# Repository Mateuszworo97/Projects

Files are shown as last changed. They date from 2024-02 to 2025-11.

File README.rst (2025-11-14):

About
-----

.. raw:: html

   <div style="text-align: justify;">

   <p>
   <strong>Apiary Water Dispensing System</strong> —  This is a device design whose purpose is to automatically supply bee water from an underground tank.
   In hard-to-reach places and with limited access to fresh water.
   The system's task is also to display current data regarding time, temperature and light intensity on the display.
   The system will enable the pump to be turned on at a specific time for a specific period of time.
   </p>

   <p>
   In the future, this project will be extended with new functionalities.
   Currently, I am working on two versions of the system that will reduce the size of the PCB and the number of components used.
   </p>

   <ul>
     <li><strong>Version 1:</strong> Uses the same components as the current version but in a smaller layout.</li>
     <li><strong>Version 2:</strong> Introduces new components to reduce PCB size while keeping the system expandable.</li>
     <li><strong>Version 3:</strong> Adds wireless data transmission using <em>LORAWAN</em> technology and integration with cloud platforms such as <em>ThingsBoard</em> or <em>TTN (The Things Network)</em>.</li>
   </ul>
   
   <p>
   One version will use the same components as the current one, but will be smaller in size.
   The second version will allow include new components that will reduce the size of the PCB board, but won't limit possibility of expended the system in the future.
   The PCB board will contains derivations for additional components that can be added later.
   The third version will expand the funtionality of the system with wireless data transmission using LORAWAN technology.
   Target of the system is to send data to cloud platform such as THINGSBOARD or TTN (The Things Network).
   Definitely, such action will investigate natural environment around device and bees activity.
   Currently, the first of version system has contributed to better understanding of bees behavior in hard to reach places with limited access to fresh water.
   I think that the third version of the system will be a great tool for beekeepers to monitor the environment around the beehive and bees activity.
   Above all, the system will allow to achieve the significant level of automation and considerably contributed to increase the capacity and coverage of the lorawan Network.
   </p>

Operation
------------

The system measures time, temperature, humidity, light intensity, battery voltage, 
value and direction of battery current flow, power consumered and delivered to battery,
Voltage of photovoltaic panel, value of photovoltaic panel.
The data is shown on the display.
By default, the pump is turned on for 1 minute. Every hour.
Using push buttons, we can increase the pump activation time from 1 to 59 minutes.
Using the buttons, we can also change the time at which the alarm will turn on (pump on).
The next time the alarm will turn on will be increased by the hour value displayed on the display.
we can delay the pump activation value from 1 to 16 hours.

Development
------------

1. Simplification 
2. Adding an automatic and manual control system
3. Enriching the project with wireless data transmission using  LORAWAN technology
4. Desiging a much smaller PCB
5. Creating own MPPT board

Block Diagram
------------
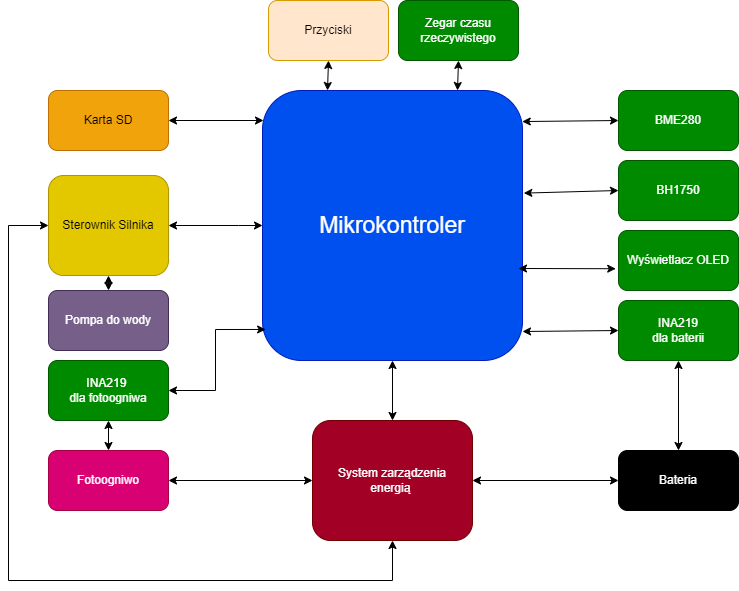
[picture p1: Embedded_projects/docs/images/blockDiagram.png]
Block Diagram


Visualization
------------
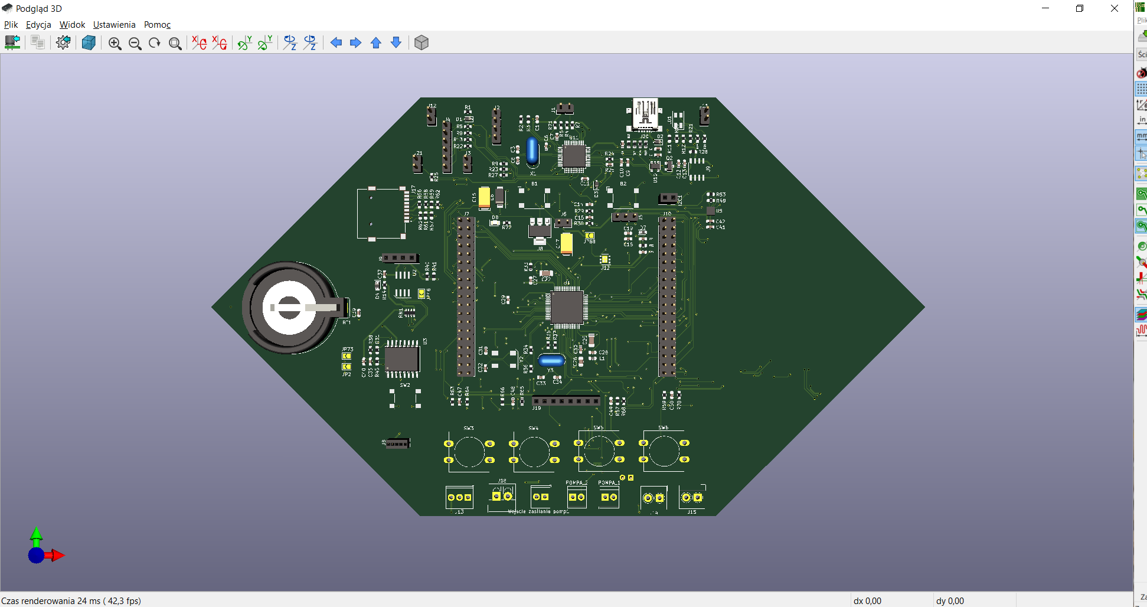
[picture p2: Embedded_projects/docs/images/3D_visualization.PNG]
Visualization


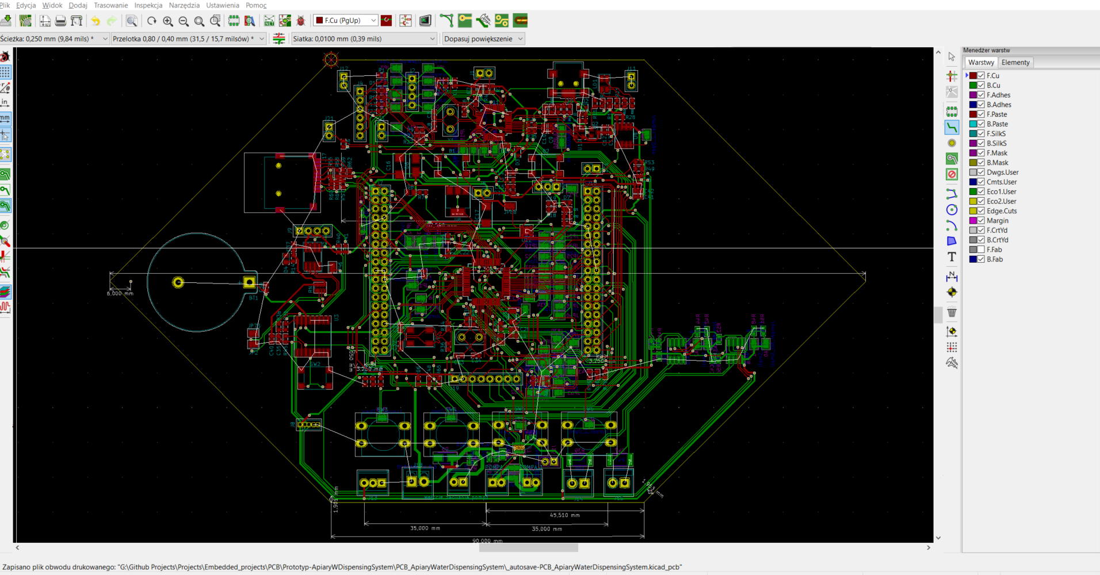
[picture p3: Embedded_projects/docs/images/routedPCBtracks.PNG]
Routed PCB tracks


Components
------------

Contains a list of components used to build the system

Refer to `docs/components.rst`.

Hardware
------------

Contains documentation of the sensors and components used.
-Diagram of the electronic system of the device.

Refer to `docs/hardware`.

Software
------------

-Diagram of the software nic system of the device.
Refer to `docs/software`.

License
------------

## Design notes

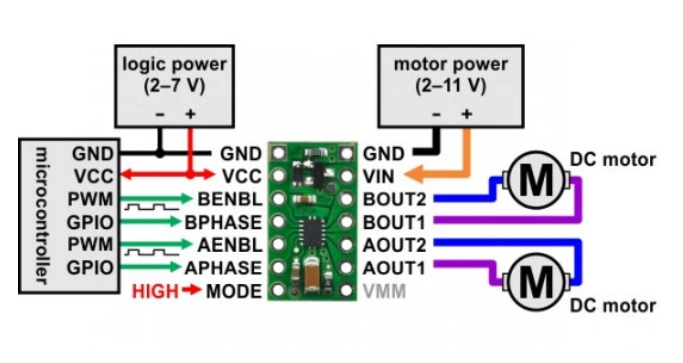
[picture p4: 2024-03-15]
Embedded_projects/docs/hardware/photos/drv8835.PNG

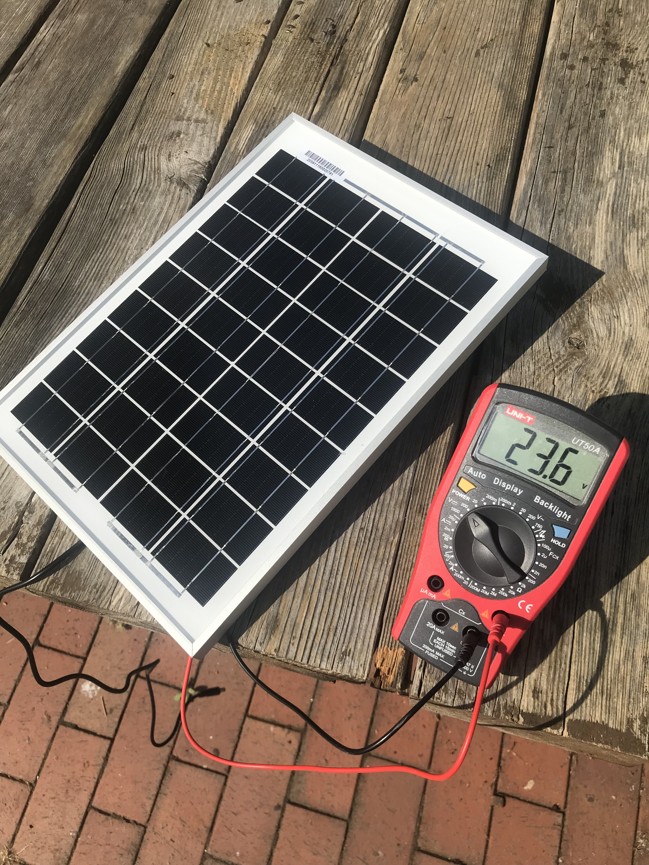
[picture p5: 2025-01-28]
Embedded_projects/docs/hardware/photos/open_circuit_pv.jpg

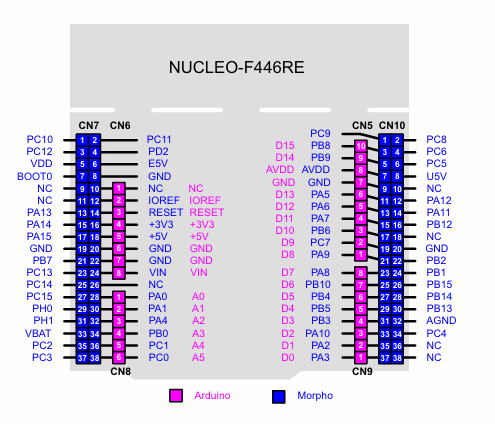
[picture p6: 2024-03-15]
Embedded_projects/docs/hardware/photos/nucleo-f446.PNG

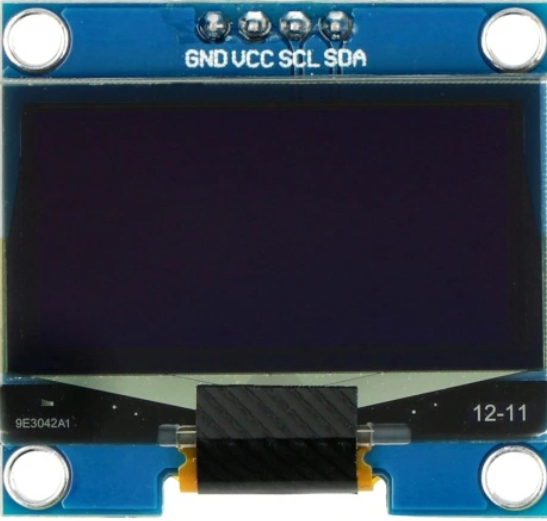
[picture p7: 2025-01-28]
Embedded_projects/docs/hardware/photos/ssd1306.PNG

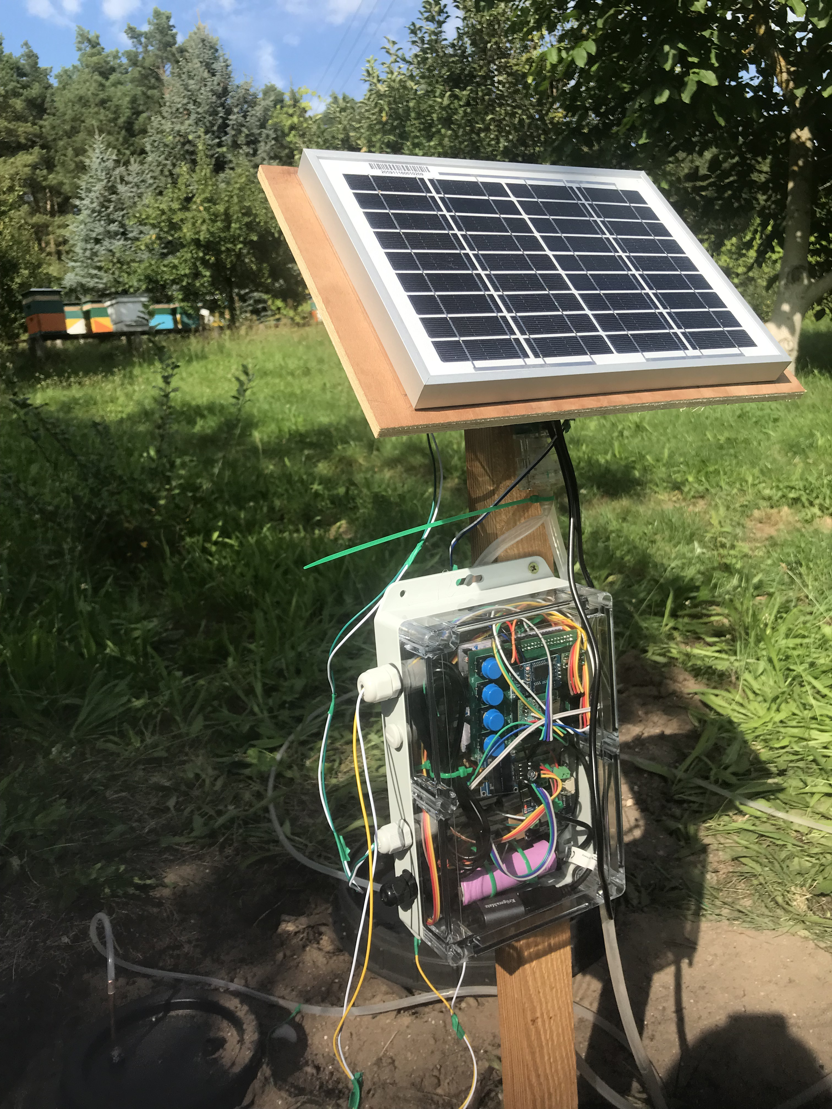
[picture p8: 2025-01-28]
Embedded_projects/docs/hardware/photos/urzadzenie_2.jpg

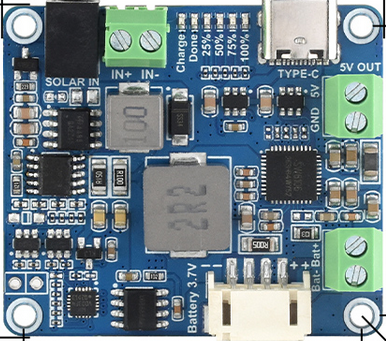
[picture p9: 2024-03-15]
Embedded_projects/docs/hardware/photos/solar_power_manager.PNG

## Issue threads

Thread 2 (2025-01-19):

Stm32WL development #4

Mateuszworo97, 2025-01-19:
the main goal of this issues will be creation project extension. Extension will be focused on long-range wireless communication, which will enable to be transferred to the cloud using a gateway device.

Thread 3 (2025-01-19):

Reducing the size of the PCB

Mateuszworo97, 2025-01-19:
the mian goal of this issue will be reduced the size of the PCB

Mateuszworo97, 2025-01-19:
- [ ]  adding two pumps connection
- [ ] control with 4 buttons
- [ ] external temperatures, humidity, pressure, light intensity sensor (Ds18b20)
- [ ] internal temperatures sensor
- [ ] SD card connector
- [ ] monitor air quality
- [ ]

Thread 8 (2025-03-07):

Switching the microcontroller to low power mode

Mateuszworo97, 2025-03-07:

Mateuszworo97, 2025-03-07:
Sleep mode advantages 👍

- [ ] retained RAM and working registers
- [ ] reduction of
- [ ] before entering sleep, suspend systick
- [ ] Sleep now (regardless of interruptions) or sleep exit (when all interrupts will be serviced)

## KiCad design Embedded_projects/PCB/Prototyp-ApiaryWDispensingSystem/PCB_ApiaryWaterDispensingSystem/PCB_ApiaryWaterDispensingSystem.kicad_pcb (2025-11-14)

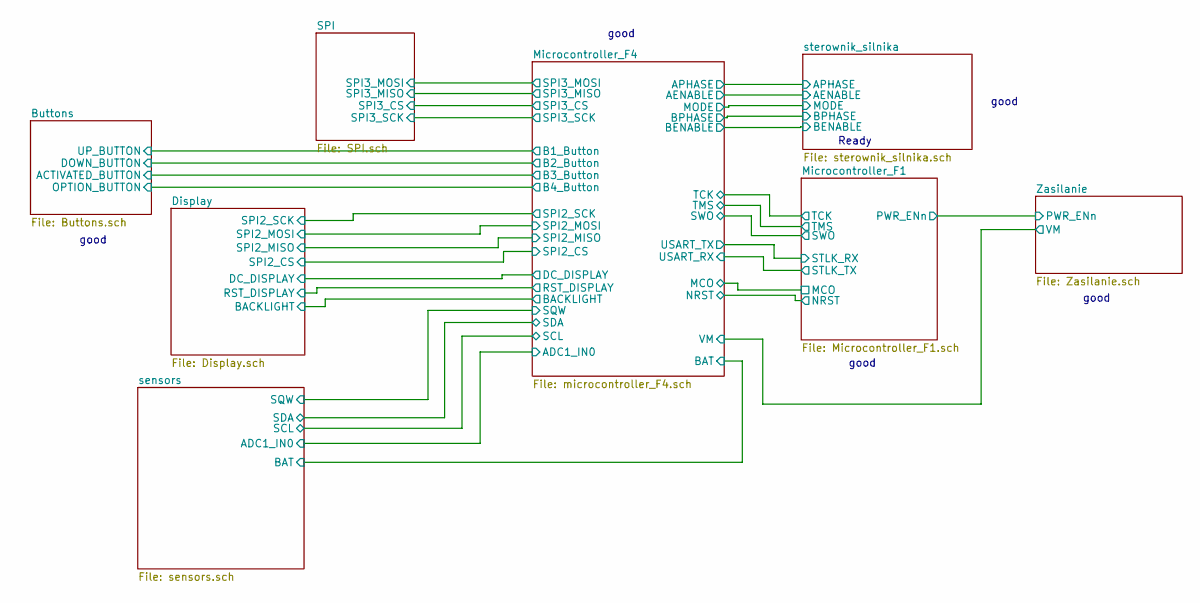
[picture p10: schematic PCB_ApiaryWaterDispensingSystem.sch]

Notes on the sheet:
Ready
good

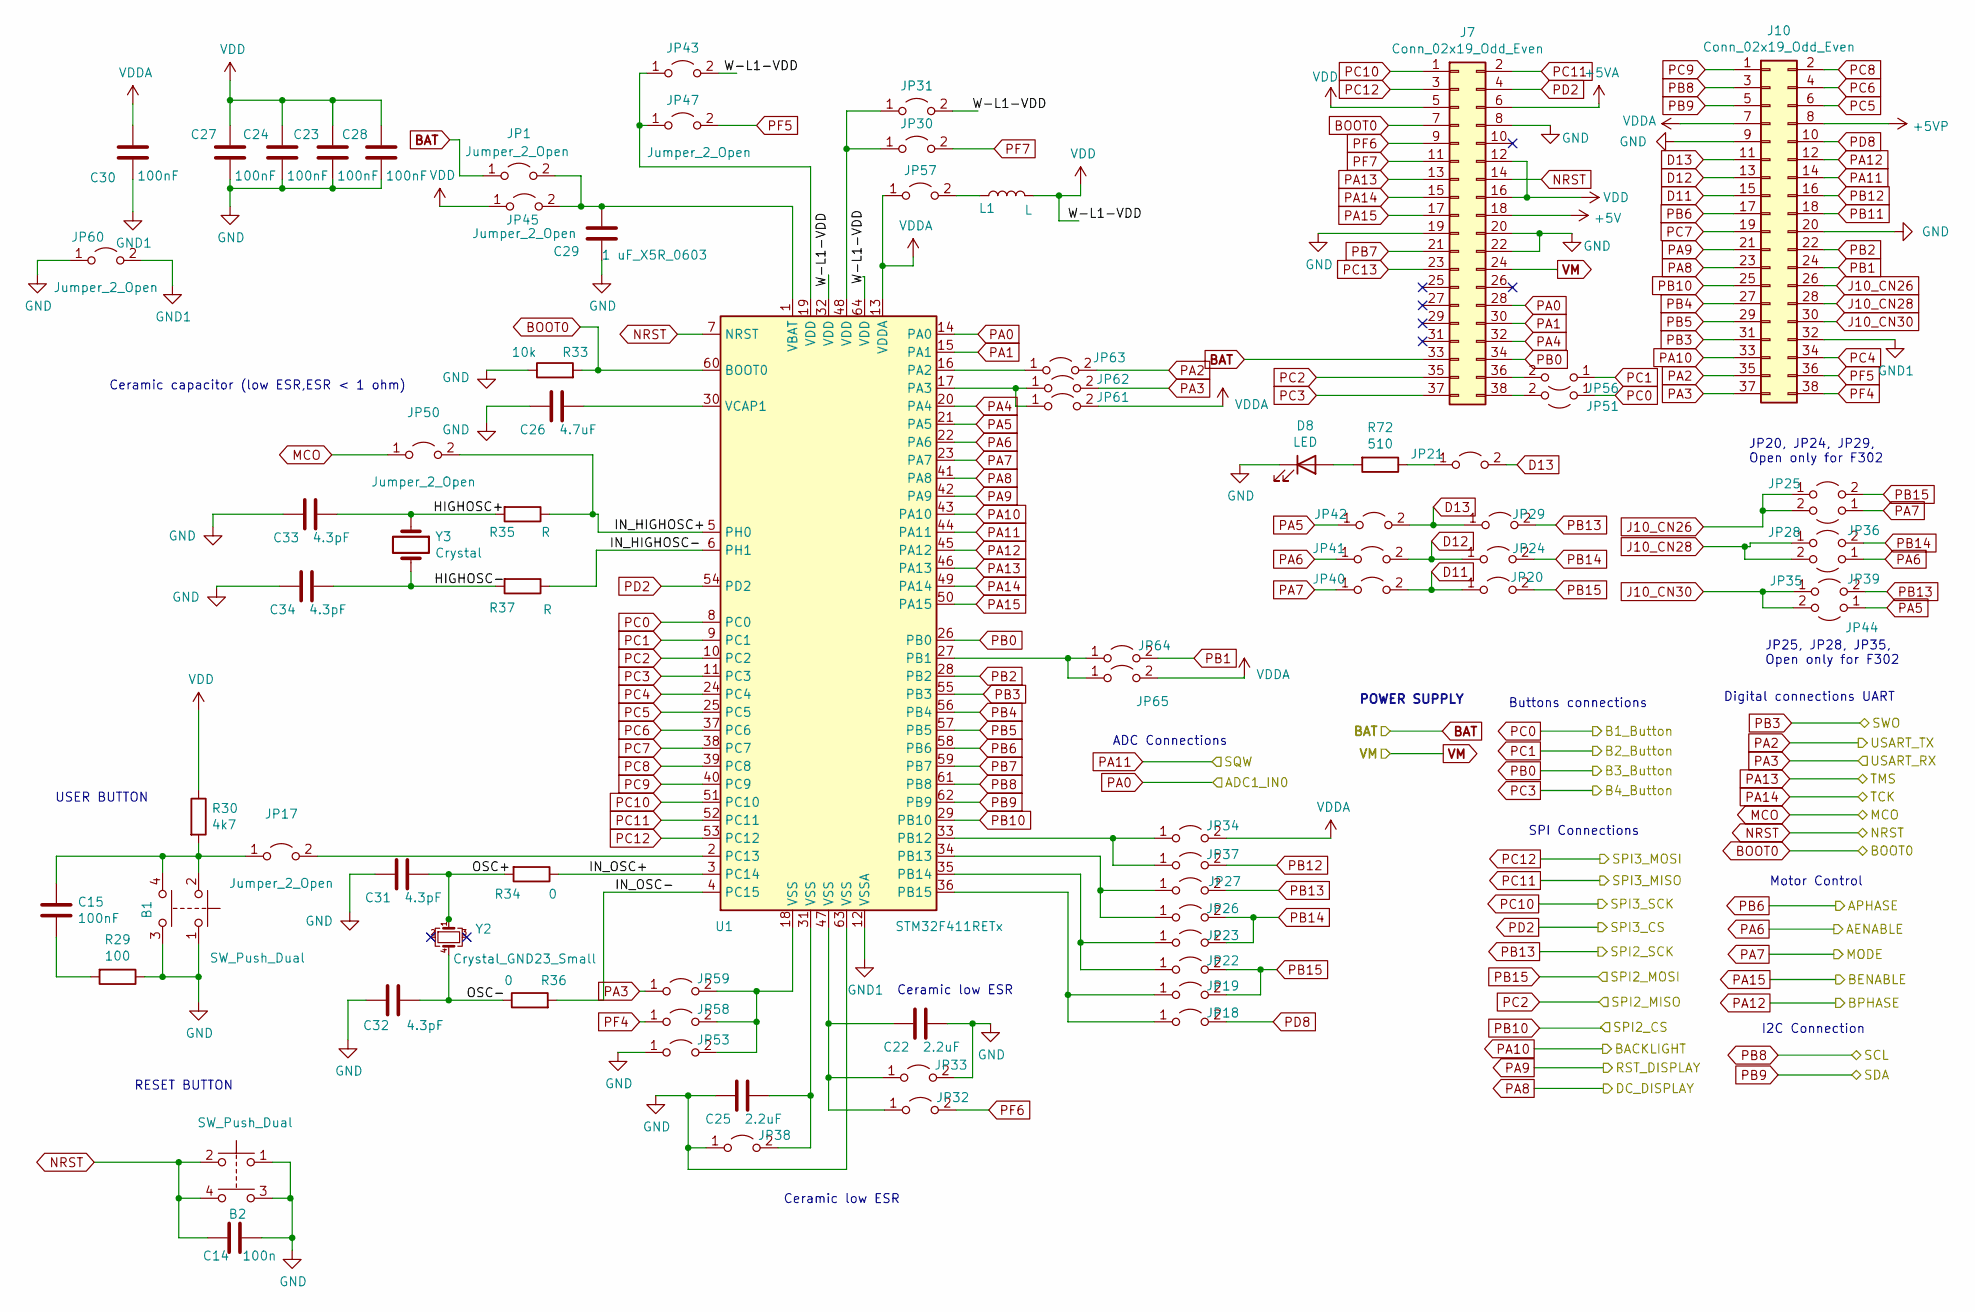
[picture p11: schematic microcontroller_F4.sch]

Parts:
B1, B2: SW_Push_Dual; SW_SPST_Omron_B3FS-100xP
C14: 100n; C_0603_1608Metric
C15, C23, C24, C27, C28, C30: 100nF; C_0603_1608Metric
C22, C25: 2.2uF; C_1206_3216Metric
C26: 4.7uF; C_0805_2012Metric
C29: 1 uF_X5R_0603; C_0603_1608Metric
C31, C32, C33, C34: 4.3pF; C_0603_1608Metric
D8: LED; LED_0805_2012Metric
J7, J10: Conn_02x19_Odd_Even; PinHeader_2x19_P2.54mm_Vertical
JP1, JP17, JP18, JP19, JP20, JP21, JP22, JP23, JP24, JP25, JP26, JP27, JP28, JP29, JP30, JP31, JP32, JP33, JP34, JP35, JP36, JP37, JP38, JP39, JP40, JP41, JP42, JP43, JP44, JP45, JP47, JP50, JP51, JP53, JP56, JP57, JP58, JP59, JP60, JP61, JP62, JP63, JP64, JP65: Jumper_2_Open; SolderJumper-2_P1.3mm_Open_TrianglePad1.0x1.5mm
L1: L; L_0603_1608Metric
R29: 100; R_0603_1608Metric
R30: 4k7; R_0603_1608Metric
R33: 10k; R_0603_1608Metric
R34, R36: 0; R_0603_1608Metric
R35, R37: R; R_0603_1608Metric
R72: 510; R_0603_1608Metric
U1: STM32F411RETx; LQFP-64_10x10mm_P0.5mm
Y2: Crystal_GND23_Small; ABS25-32768KHZ-6-T_Abracon
Y3: Crystal; Resonator-2Pin_W8.0mm_H3.5mm

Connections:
+5V: J7.18; also elsewhere on the board
+5VA: J7.6; also elsewhere on the board
+5VP: J10.8; also elsewhere on the board
/Microcontroller_F4/HIGHOSC+: C33.1, R35.2, Y3.1
/Microcontroller_F4/HIGHOSC-: C34.1, R37.2, Y3.2
/Microcontroller_F4/IN_HIGHOSC+: JP50.2 (B), R35.1, U1.5 (PH0)
/Microcontroller_F4/IN_HIGHOSC-: R37.1, U1.6 (PH1)
/Microcontroller_F4/IN_OSC+: R34.1, U1.3 (PC14)
/Microcontroller_F4/IN_OSC-: R36.2, U1.4 (PC15)
/Microcontroller_F4/OSC+: C31.1, R34.2, Y2.1
/Microcontroller_F4/OSC-: C32.1, R36.1, Y2.4
ADC1_IN0: J7.28, U1.14 (PA0); also elsewhere on the board
AENABLE: JP39.1 (A), JP41.1 (A), U1.22 (PA6); also elsewhere on the board
APHASE: J10.17, U1.58 (PB6); also elsewhere on the board
BAT: J7.33, JP1.1 (A); also elsewhere on the board
BENABLE: J7.17, U1.50 (PA15); also elsewhere on the board
BOOT0: J7.7, R33.2, U1.60 (BOOT0); also elsewhere on the board
BPHASE: J10.12, U1.45 (PA12); also elsewhere on the board
Backlight: J10.33, U1.43 (PA10); also elsewhere on the board
CLK: J7.1, U1.51 (PC10); also elsewhere on the board
CMD: J7.3, U1.53 (PC12); also elsewhere on the board
D11: J10.15, JP20.1 (A), JP40.2 (B)
D12: J10.13, JP24.1 (A), JP41.2 (B)
D13: J10.11, JP21.2 (B), JP29.1 (A), JP42.2 (B)
DAT0: J7.2, U1.52 (PC11); also elsewhere on the board
DAT3: J7.4, U1.54 (PD2); also elsewhere on the board
DC_DISPLAY: J10.23, U1.41 (PA8); also elsewhere on the board
GND: B1.1, B1.3, B2.1, B2.3, C14.1, C22.1, C23.1, C24.1, C25.2, C26.2, C27.1, C28.1, C29.1, C31.2, C32.2, C33.2, C34.2, D8.1 (K), J7.8, J7.19, J7.20, J7.22, J10.9, J10.20, JP33.2 (B), JP38.1 (A), JP53.1 (A), JP60.1 (A), R29.1, R33.1, U1.63 (VSS); also elsewhere on the board
GND1: C30.1, J10.32, JP60.2 (B), U1.12 (VSSA)
J10_CN26: J10.26, JP25.1 (A), JP36.2 (B)
J10_CN28: J10.28, JP28.1 (A), JP39.2 (B)
J10_CN30: J10.30, JP35.1 (A), JP44.2 (B)
MCO: JP50.1 (A); also elsewhere on the board
MODE: JP36.1 (A), JP40.1 (A), U1.23 (PA7); also elsewhere on the board
NRST: B2.2, B2.4, C14.2, J7.14, U1.7 (NRST); also elsewhere on the board
unnamed: B1.2, B1.4, C15.1, JP17.1 (A), R30.2
unnamed: C15.2, R29.2
unnamed: C22.2, JP32.1 (A), JP33.1 (A), U1.47 (VSS)
unnamed: C25.1, JP38.2 (B), U1.31 (VSS)
unnamed: C26.1, U1.30 (VCAP1)
unnamed: C29.2, JP1.2 (B), JP45.2 (B), U1.1 (VBAT)
unnamed: D8.2 (A), R72.2
unnamed: J7.36, JP56.2 (B)
unnamed: J7.38, JP51.2 (B)
unnamed: JP17.2 (B), U1.2 (PC13)
unnamed: JP18.1 (A), JP19.1 (A), U1.36 (PB15)
unnamed: JP21.1 (A), R72.1
unnamed: JP22.1 (A), JP23.1 (A), U1.35 (PB14)
unnamed: JP26.1 (A), JP27.1 (A), U1.34 (PB13)
unnamed: JP30.1 (A), JP31.1 (A), U1.48 (VDD)
unnamed: JP34.1 (A), JP37.1 (A), U1.33 (PB12)
unnamed: JP43.1 (A), JP47.1 (A), U1.19 (VDD)
unnamed: JP53.2 (B), JP58.2 (B), JP59.2 (B), U1.18 (VSS)
unnamed: JP57.2 (B), L1.1
unnamed: JP61.1 (A), JP62.1 (A), U1.17 (PA3)
unnamed: JP63.1 (A), U1.16 (PA2)
unnamed: JP64.1 (A), JP65.1 (A), U1.27 (PB1)
PA1: J7.30, U1.15 (PA1)
PA2: J10.35, JP63.2 (B); also elsewhere on the board
PA3: J10.37, JP59.1 (A), JP62.2 (B); also elsewhere on the board
PA4: J7.32, U1.20 (PA4)
PA5: JP42.1 (A), JP44.1 (A), U1.21 (PA5)
PA9: J10.21, U1.42 (PA9); also elsewhere on the board
PA11: J10.14, U1.44 (PA11); also elsewhere on the board
PA13: J7.13, U1.46 (PA13); also elsewhere on the board
PA14: J7.15, U1.49 (PA14); also elsewhere on the board
PB0: J7.34, U1.26 (PB0); also elsewhere on the board
PB1: J10.24, JP64.2 (B)
PB2: J10.22, U1.28 (PB2)
PB3: J10.31, U1.55 (PB3); also elsewhere on the board
PB4: J10.27, U1.56 (PB4)
PB5: J10.29, U1.57 (PB5)
PB7: J7.21, U1.59 (PB7)
PB8: J10.3, U1.61 (PB8); also elsewhere on the board
PB9: J10.5, U1.62 (PB9); also elsewhere on the board
PB10: J10.25, U1.29 (PB10); also elsewhere on the board
PB12: J10.16, JP37.2 (B)
PB13: JP27.2 (B), JP29.2 (B), JP35.2 (B); also elsewhere on the board
PB14: JP23.2 (B), JP24.2 (B), JP26.2 (B), JP28.2 (B)
PB15: JP19.2 (B), JP20.2 (B), JP22.2 (B), JP25.2 (B); also elsewhere on the board
PC0: JP51.1 (A), U1.8 (PC0); also elsewhere on the board
PC1: JP56.1 (A), U1.9 (PC1); also elsewhere on the board
PC2: J7.35, U1.10 (PC2)
PC3: J7.37, U1.11 (PC3); also elsewhere on the board
PC4: J10.34, U1.24 (PC4)
PC5: J10.6, U1.25 (PC5)
PC6: J10.4, U1.37 (PC6)
PC7: J10.19, U1.38 (PC7)
PC8: J10.2, U1.39 (PC8)
PC9: J10.1, U1.40 (PC9)
PD8: J10.10, JP18.2 (B)
PF4: J10.38, JP58.1 (A)
PF5: J10.36, JP47.2 (B)
PF6: J7.9, JP32.2 (B)
PF7: J7.11, JP30.2 (B)
VDD: C23.2, C24.2, C27.2, C28.2, J7.5, J7.12, J7.16, JP31.2 (B), JP43.2 (B), JP45.1 (A), L1.2, R30.1, U1.32 (VDD), U1.64 (VDD); also elsewhere on the board
VDDA: C30.2, J10.7, JP34.2 (B), JP57.1 (A), JP61.2 (B), JP65.2 (B), U1.13 (VDDA)
VM: J7.24; also elsewhere on the board

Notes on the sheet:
Ceramic capacitor (low ESR,ESR < 1 ohm)
Ceramic low ESR
RESET BUTTON
USER BUTTON
Buttons connections
Digital connections UART
SPI Connections
Motor Control
I2C Connection
JP25, JP28, JP35, Open only for F302
JP20, JP24, JP29, Open only for F302
POWER SUPPLY
ADC Connections

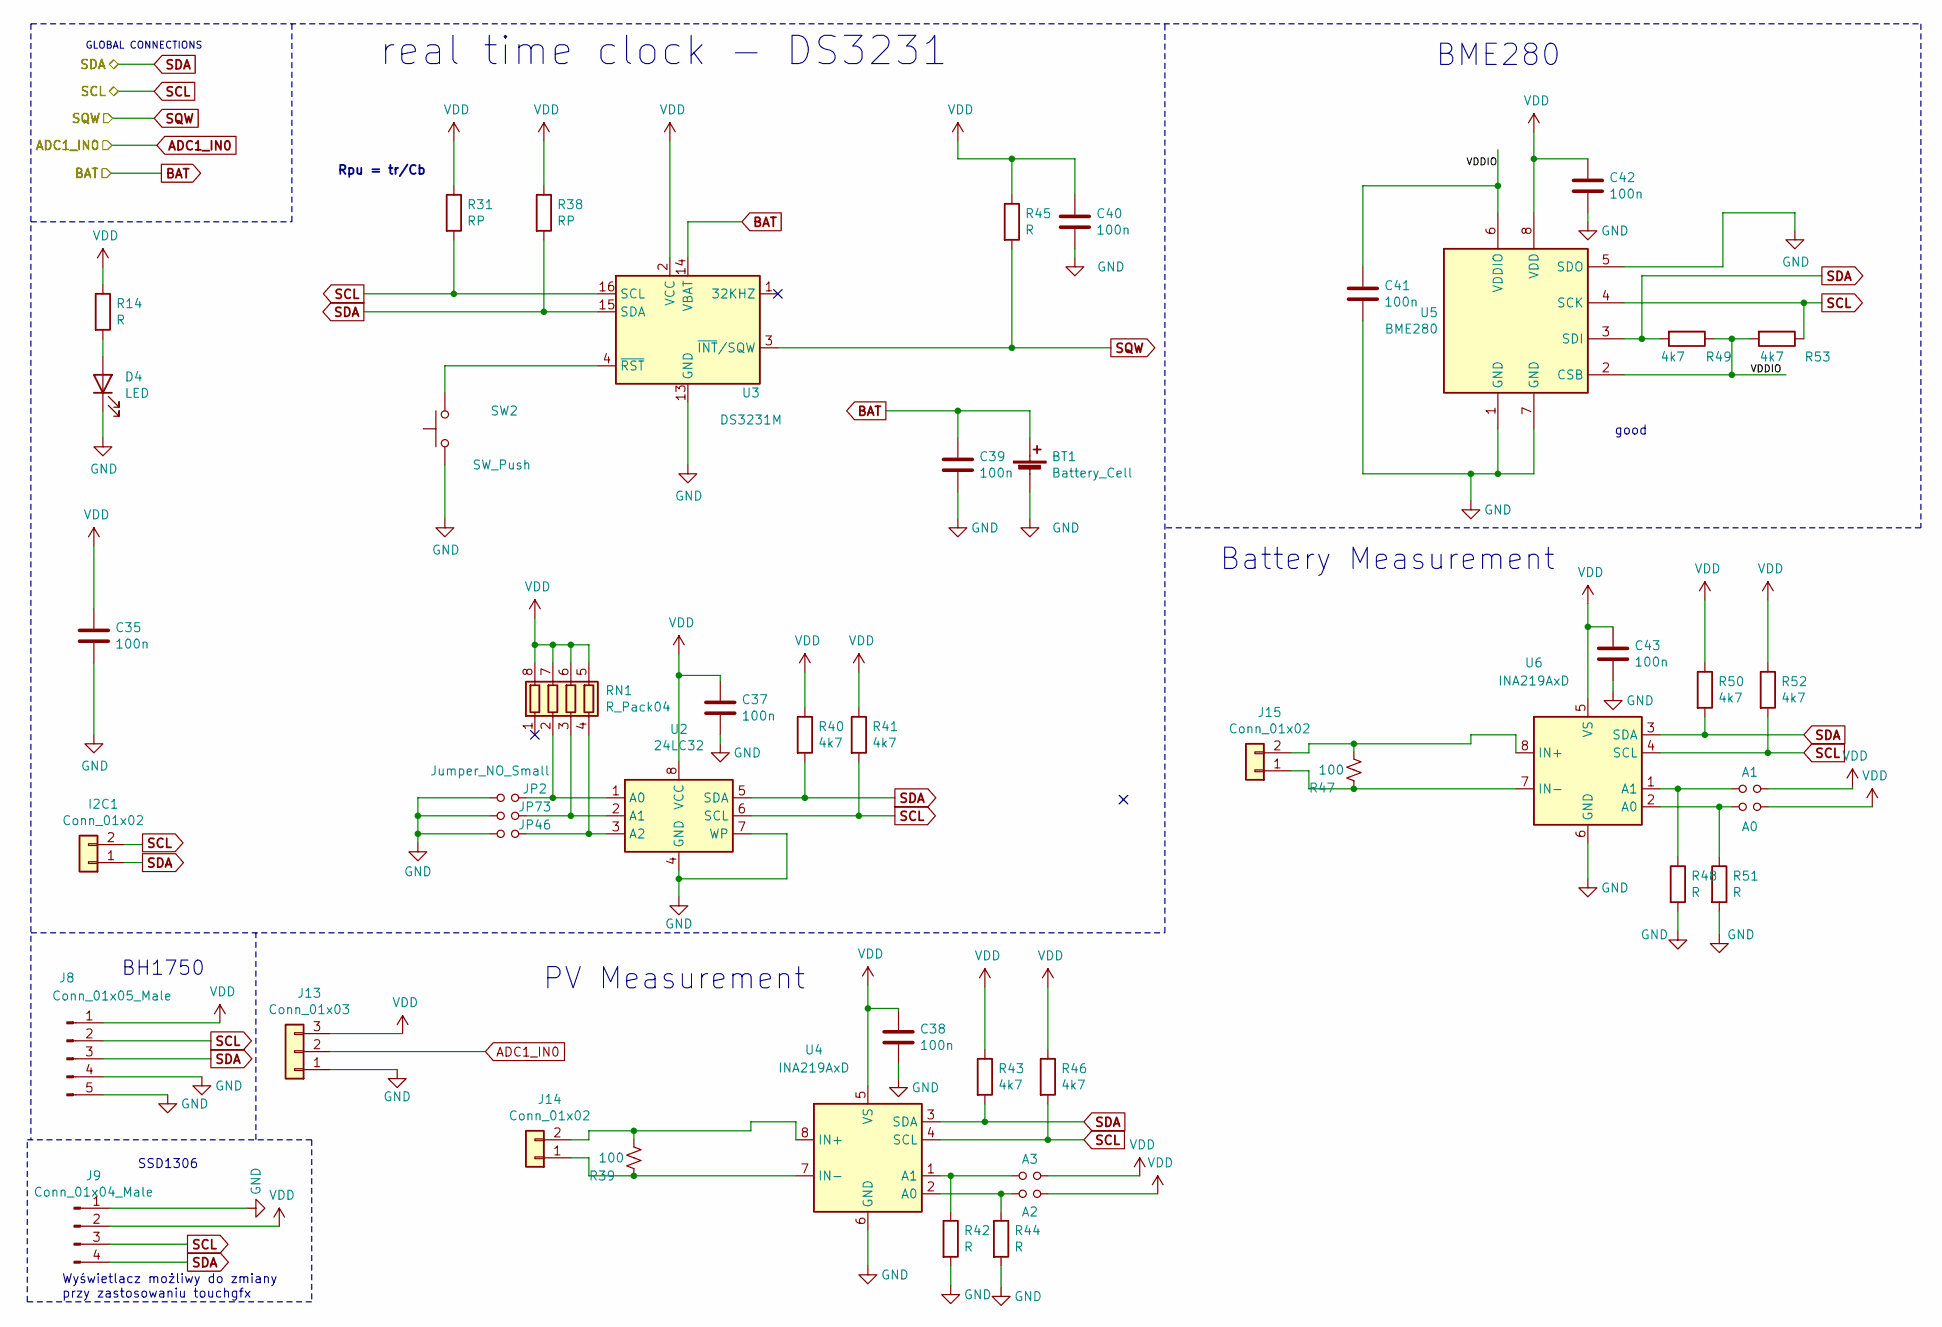
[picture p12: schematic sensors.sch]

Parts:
A0, A1, A2, A3: Jumper_NO_Small; SolderJumper-2_P1.3mm_Open_TrianglePad1.0x1.5mm
BT1: Battery_Cell; BatteryHolder_Keystone_107_1x23mm
C35, C37, C38, C39, C40, C41, C42, C43: 100n; C_0603_1608Metric
D4: LED; D_0805_2012Metric
I2C1: Conn_01x02; PinSocket_1x02_P2.54mm_Vertical
J8: Conn_01x05_Male; PinSocket_1x05_P1.27mm_Vertical
J9: Conn_01x04_Male; PinSocket_1x04_P2.54mm_Vertical
J13: Conn_01x03; TerminalBlock_TE_282834-3_1x03_P2.54mm_Horizontal
J14, J15: Conn_01x02; TerminalBlock_4Ucon_1x02_P3.50mm_Horizontal
JP2, JP46, JP73: Jumper_NO_Small; SolderJumper-2_P1.3mm_Open_TrianglePad1.0x1.5mm
R14, R42, R44, R45, R48, R51: R; R_0603_1608Metric
R31, R38: RP; R_0603_1608Metric
R39, R47: 100; R_2512_6332Metric
R40, R41, R43, R46, R49, R50, R52, R53: 4k7; R_0603_1608Metric
RN1: R_Pack04; R_Array_Convex_4x0603
SW2: SW_Push; SW_Push_1P1T_NO_6x6mm_H9.5mm
U2: 24LC32
U3: DS3231M; SOIC-16W_7.5x10.3mm_P1.27mm
U4, U6: INA219AxD; SOIC-8_3.9x4.9mm_P1.27mm
U5: BME280; Bosch_LGA-8_2.5x2.5mm_P0.65mm_ClockwisePinNumbering

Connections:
/sensors/VDDIO: C41.1, R49.1, R53.2, U5.2 (CSB), U5.6 (VDDIO)
ADC1_IN0: J13.2; also elsewhere on the board
BAT: BT1.1 (+), C39.1, U3.14 (VBAT); also elsewhere on the board
GND: BT1.2 (-), C35.2, C37.2, C38.2, C39.2, C40.2, C41.2, C42.2, C43.2, D4.1 (K), J8.4, J8.5, J9.1, J13.1, JP2.1, JP46.1, JP73.1, R42.2, R44.2, R48.2, R51.2, SW2.1, U2.4 (GND), U2.7 (WP), U3.5 (GND), U3.6 (GND), U3.7 (GND), U3.8 (GND), U3.9 (GND), U3.10 (GND), U3.11 (GND), U3.12 (GND), U3.13 (GND), U4.6 (GND), U5.1 (GND), U5.5 (SDO), U5.7 (GND), U6.6 (GND); also elsewhere on the board
unnamed: A0.1, R51.1, U6.2 (A0)
unnamed: A1.1, R48.1, U6.1 (A1)
unnamed: A2.1, R44.1, U4.2 (A0)
unnamed: A3.1, R42.1, U4.1 (A1)
unnamed: D4.2 (A), R14.2
unnamed: J14.1, R39.1, U4.7 (IN-)
unnamed: J14.2, R39.2, U4.8 (IN+)
unnamed: J15.1, R47.1, U6.7 (IN-)
unnamed: J15.2, R47.2, U6.8 (IN+)
unnamed: JP2.2, RN1.2 (R2.1), U2.1 (A0)
unnamed: JP46.2, RN1.4 (R4.1), U2.3 (A2)
unnamed: JP73.2, RN1.3 (R3.1), U2.2 (A1)
unnamed: SW2.2, U3.4 (~RST)
PA11: R45.2, U3.3 (~INT~/SQW); also elsewhere on the board
PB8: I2C1.2, J8.2, J9.3, R31.2, R41.2, R46.2, R52.2, R53.1, U2.6 (SCL), U3.16 (SCL), U4.4 (SCL), U5.4 (SCK), U6.4 (SCL); also elsewhere on the board
PB9: I2C1.1, J8.3, J9.4, R38.2, R40.2, R43.2, R49.2, R50.2, U2.5 (SDA), U3.15 (SDA), U4.3 (SDA), U5.3 (SDI), U6.3 (SDA); also elsewhere on the board
VDD: A0.2, A1.2, A2.2, A3.2, C35.1, C37.1, C38.1, C40.1, C42.1, C43.1, J8.1, J9.2, J13.3, R14.1, R31.1, R38.1, R40.1, R41.1, R43.1, R45.1, R46.1, R50.1, R52.1, RN1.5 (R4.2), RN1.6 (R3.2), RN1.7 (R2.2), RN1.8 (R1.2), U2.8 (VCC), U3.2 (VCC), U4.5 (VS), U5.8 (VDD), U6.5 (VS); also elsewhere on the board

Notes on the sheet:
real time clock - DS3231
Rpu = tr/Cb
BME280
GLOBAL CONNECTIONS
BH1750
Battery Measurement
PV Measurement
SSD1306
Wyświetlacz możliwy do zmiany przy zastosowaniu touchgfx
good

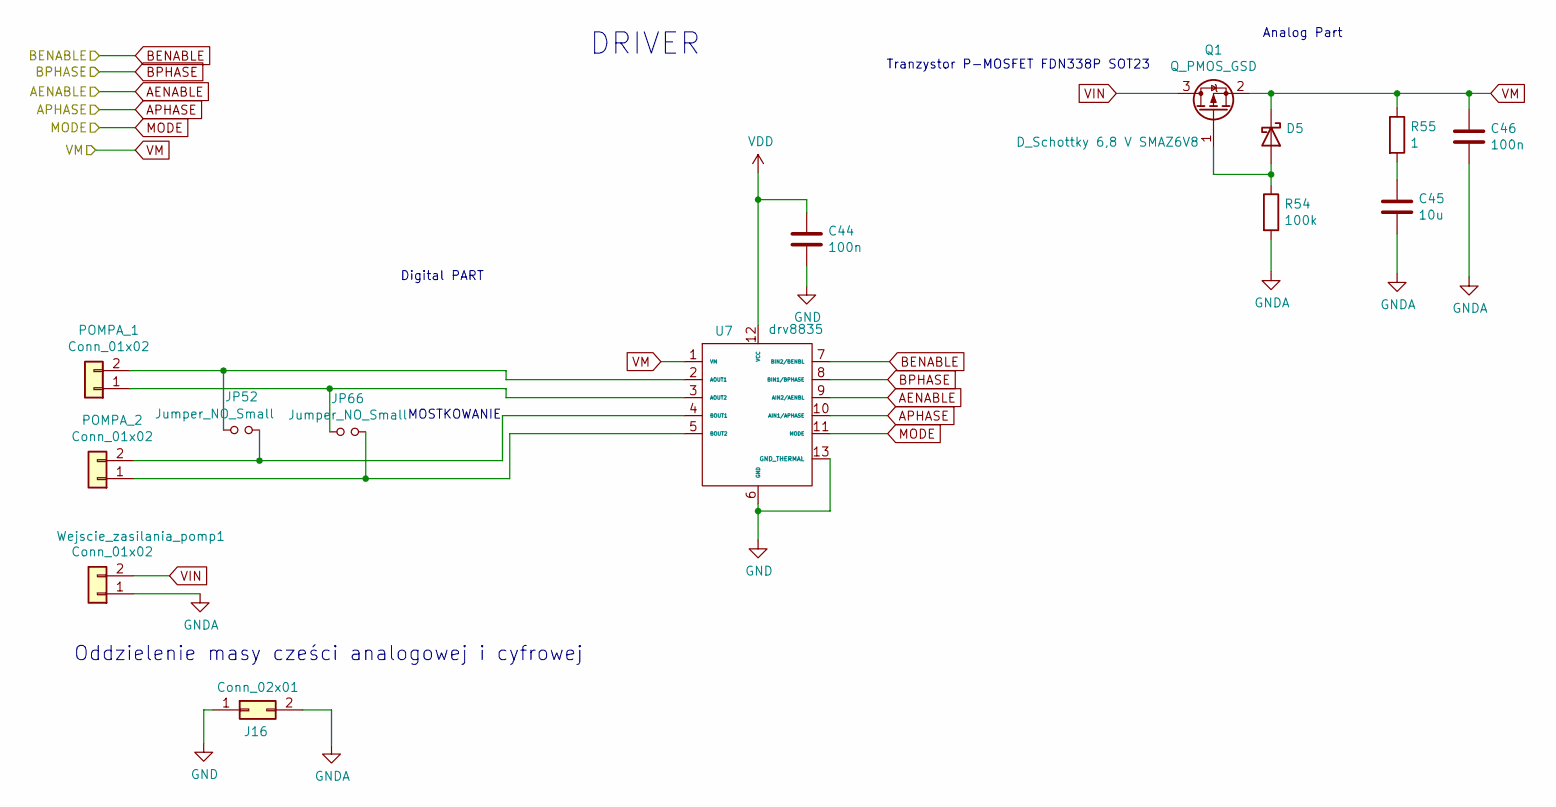
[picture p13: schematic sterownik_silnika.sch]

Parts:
C44, C46: 100n; C_0603_1608Metric
C45: 10u; C_0805_2012Metric
D5: D_Schottky 6,8 V SMAZ6V8; D_SMA
J16: Conn_02x01; PinHeader_1x02_P2.54mm_Vertical
JP52, JP66: Jumper_NO_Small; SolderJumper-2_P1.3mm_Open_TrianglePad1.0x1.5mm
POMPA_1, POMPA_2: Conn_01x02; TerminalBlock_TE_282834-2_1x02_P2.54mm_Horizontal
Q1: Q_PMOS_GSD; SOT-23
R54: 100k; R_0603_1608Metric
R55: 1; R_0603_1608Metric
U7: drv8835; WSON-12-1EP_3x2mm_P0.5mm_EP1x2.65_ThermalVias
Wejscie_zasilania_pomp1: Conn_01x02; TerminalBlock_TE_282834-2_1x02_P2.54mm_Horizontal

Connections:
AENABLE: U7.9 (AIN2/AENBL); also elsewhere on the board
APHASE: U7.10 (AIN1/APHASE); also elsewhere on the board
BENABLE: U7.7 (BIN2/BENBL); also elsewhere on the board
BPHASE: U7.8 (BIN1/BPHASE); also elsewhere on the board
GND: C44.2, J16.1, U7.6 (GND), U7.13 (GND_THERMAL); also elsewhere on the board
GNDA: C45.2, C46.2, J16.2, R54.2, Wejscie_zasilania_pomp1.1
MODE: U7.11 (MODE); also elsewhere on the board
unnamed: C45.1, R55.2
unnamed: D5.2 (A), Q1.1 (G), R54.1
unnamed: JP52.1, POMPA_1.2, U7.2 (AOUT1)
unnamed: JP52.2, POMPA_2.2, U7.4 (BOUT1)
unnamed: JP66.1, POMPA_1.1, U7.3 (AOUT2)
unnamed: JP66.2, POMPA_2.1, U7.5 (BOUT2)
VDD: C44.1, U7.12 (VCC); also elsewhere on the board
VIN: Q1.3 (D), Wejscie_zasilania_pomp1.2
VM: C46.1, D5.1 (K), Q1.2 (S), R55.1, U7.1 (VM); also elsewhere on the board

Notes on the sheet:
DRIVER
MOSTKOWANIE
Oddzielenie masy cześci analogowej i cyfrowej
Digital PART
Analog Part
Tranzystor P-MOSFET FDN338P SOT23

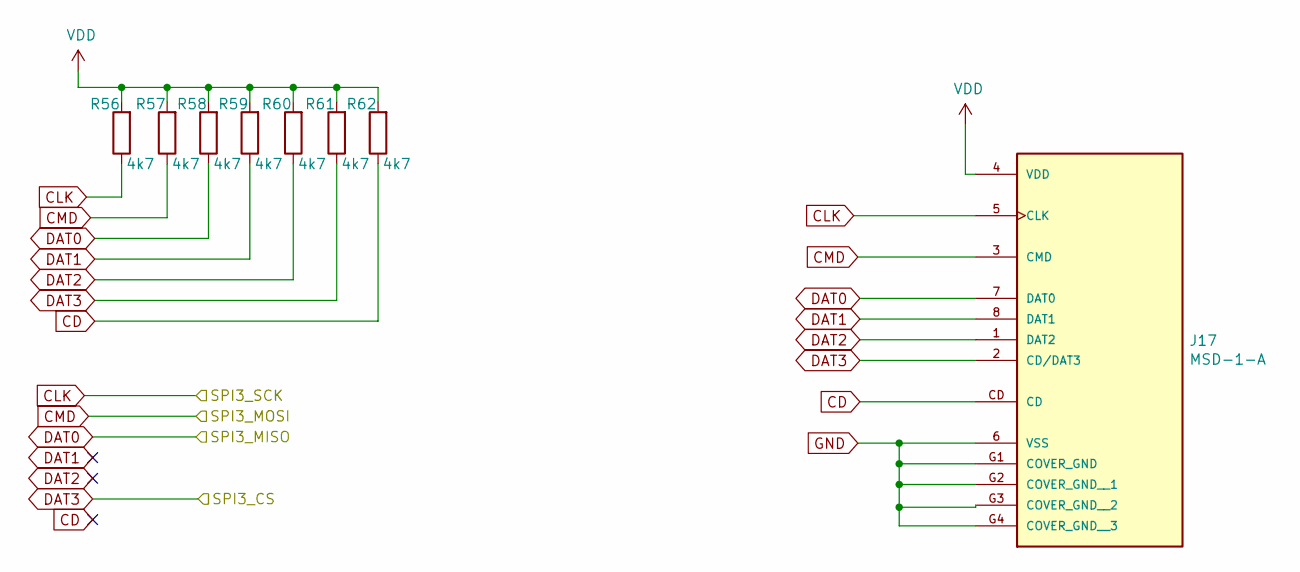
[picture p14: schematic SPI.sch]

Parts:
J17: MSD-1-A; CUI_MSD-1-A; PARTREV 1.0
R56, R57, R58, R59, R60, R61, R62: 4k7; R_0603_1608Metric

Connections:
CD: J17.CD, R62.1
CLK: J17.5 (CLK), R56.1; also elsewhere on the board
CMD: J17.3 (CMD), R57.1; also elsewhere on the board
DAT0: J17.7 (DAT0), R58.1; also elsewhere on the board
DAT1: J17.8 (DAT1), R59.1
DAT2: J17.1 (DAT2), R60.1
DAT3: J17.2 (CD/DAT3), R61.1; also elsewhere on the board
GND: J17.6 (VSS), J17.G1 (COVER_GND), J17.G2 (COVER_GND__1), J17.G3 (COVER_GND__2), J17.G4 (COVER_GND__3); also elsewhere on the board
VDD: J17.4 (VDD), R56.2, R57.2, R58.2, R59.2, R60.2, R61.2, R62.2; also elsewhere on the board

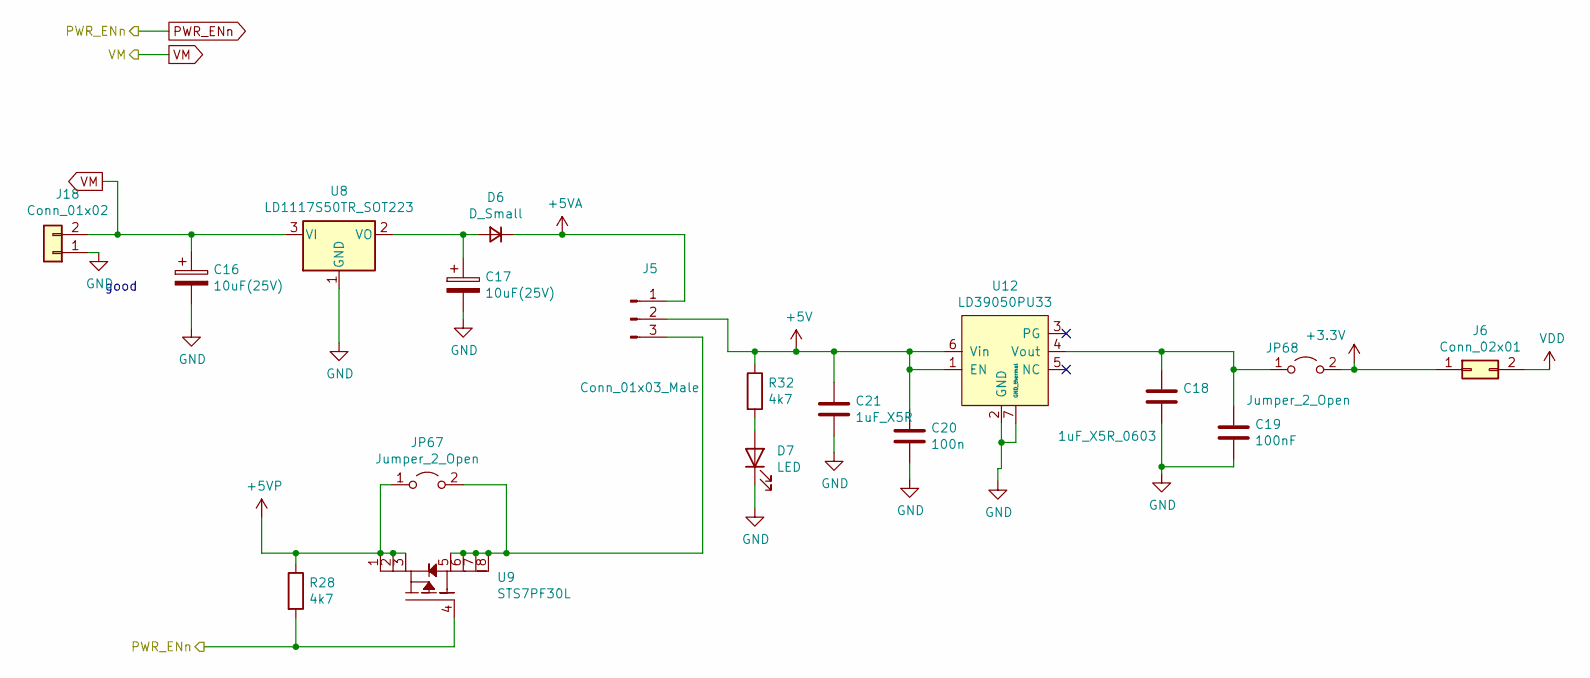
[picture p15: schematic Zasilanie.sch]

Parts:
C16, C17: 10uF(25V); CP_EIA-6032-15_Kemet-U
C18: 1uF_X5R_0603; C_0603_1608Metric
C19: 100nF; C_0603_1608Metric
C20: 100n; C_0603_1608Metric
C21: 1uF_X5R; C_0603_1608Metric
D6: D_Small; D_SMA
D7: LED; D_0603_1608Metric
J5: Conn_01x03_Male; PinHeader_1x03_P2.54mm_Vertical
J6: Conn_02x01; PinHeader_1x02_P2.54mm_Vertical
J18: Conn_01x02; TerminalBlock_4Ucon_1x02_P3.50mm_Vertical
JP67, JP68: Jumper_2_Open; SolderJumper-2_P1.3mm_Open_TrianglePad1.0x1.5mm
R28, R32: 4k7; R_0603_1608Metric
U8: LD1117S50TR_SOT223; SOT-223-3_TabPin2
U9: STS7PF30L; SO-8_3.9x4.9mm_P1.27mm
U12: LD39050PU33; WSON-6-1EP_3x3mm_P0.95mm

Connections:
+5V: C20.1, C21.1, J5.2, R32.1, U12.1 (EN), U12.6 (Vin); also elsewhere on the board
+5VA: D6.1 (K), J5.1; also elsewhere on the board
+5VP: JP67.1 (A), R28.1, U9.1, U9.2, U9.3; also elsewhere on the board
GND: C16.2, C17.2, C18.2, C19.2, C20.2, C21.2, D7.1 (K), J18.1, U8.1 (GND), U12.2 (GND), U12.7 (GND_thermal); also elsewhere on the board
unnamed: C17.1, D6.2 (A), U8.2 (VO)
unnamed: C18.1, C19.1, JP68.1 (A), U12.4 (Vout)
unnamed: D7.2 (A), R32.2
unnamed: J5.3, JP67.2 (B), U9.5, U9.6, U9.7, U9.8
PWR_ENn: R28.2, U9.4; also elsewhere on the board
VDD: J6.2; also elsewhere on the board
VM: C16.1, J18.2, U8.3 (VI); also elsewhere on the board

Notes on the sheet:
good

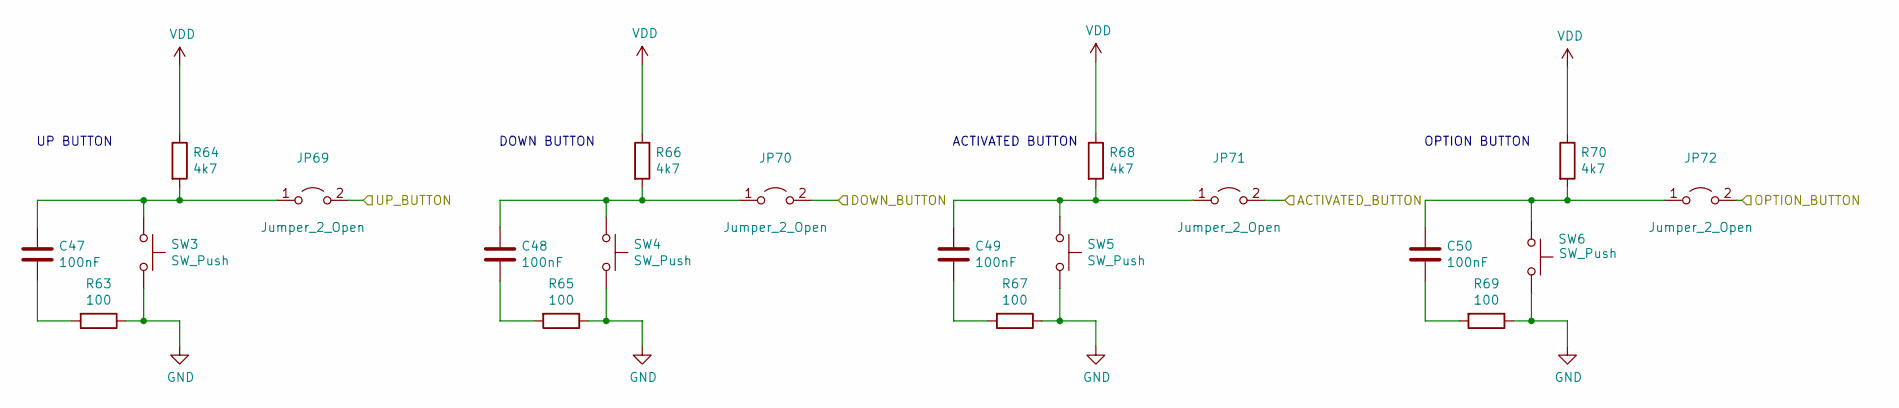
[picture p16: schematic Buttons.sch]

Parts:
C47, C48, C49, C50: 100nF; C_0603_1608Metric
JP69, JP70, JP71, JP72: Jumper_2_Open; SolderJumper-2_P1.3mm_Open_TrianglePad1.0x1.5mm
R63, R65, R67, R69: 100; R_0603_1608Metric
R64, R66, R68, R70: 4k7; R_0603_1608Metric
SW3, SW4, SW5, SW6: SW_Push; SW_PUSH-12mm

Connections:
GND: R63.1, R65.1, R67.1, R69.1, SW3.2, SW4.2, SW5.2, SW6.2; also elsewhere on the board
unnamed: C47.1, JP69.1 (A), R64.2, SW3.1
unnamed: C47.2, R63.2
unnamed: C48.1, JP70.1 (A), R66.2, SW4.1
unnamed: C48.2, R65.2
unnamed: C49.1, JP71.1 (A), R68.2, SW5.1
unnamed: C49.2, R67.2
unnamed: C50.1, JP72.1 (A), R70.2, SW6.1
unnamed: C50.2, R69.2
PB0: JP71.2 (B); also elsewhere on the board
PC0: JP69.2 (B); also elsewhere on the board
PC1: JP70.2 (B); also elsewhere on the board
PC3: JP72.2 (B); also elsewhere on the board
VDD: R64.1, R66.1, R68.1, R70.1; also elsewhere on the board

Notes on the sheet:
UP BUTTON
DOWN BUTTON
ACTIVATED BUTTON
OPTION BUTTON

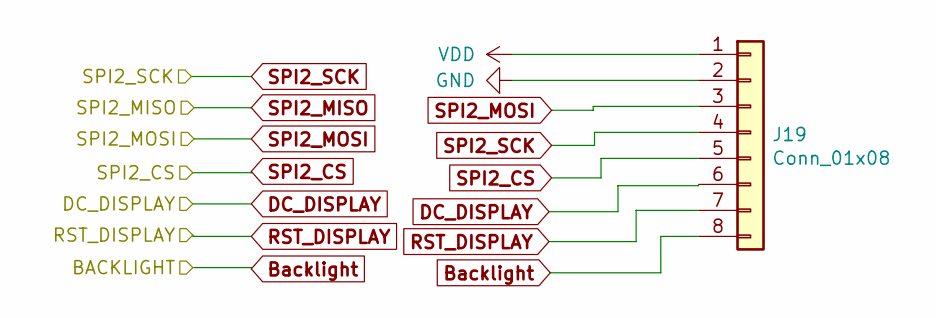
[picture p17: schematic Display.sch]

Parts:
J19: Conn_01x08; PinSocket_1x08_P2.54mm_Vertical

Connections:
Backlight: J19.8; also elsewhere on the board
DC_DISPLAY: J19.6; also elsewhere on the board
GND: J19.2; also elsewhere on the board
PA9: J19.7; also elsewhere on the board
PB10: J19.5; also elsewhere on the board
PB13: J19.4; also elsewhere on the board
PB15: J19.3; also elsewhere on the board
VDD: J19.1; also elsewhere on the board

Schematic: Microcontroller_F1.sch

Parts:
C1, C4, C5, C6, C7, C11, C12: 100n; C_0603_1608Metric
C2, C13: 1uF_X5R_0603; C_0603_1608Metric
C3, C8, C10: 20pF; C_0603_1608Metric
C9: 10nF_X7R; C_0603_1608Metric
D1, D2, D3: BAT60A; D_SOD-323
J1, J3, J11, J12, J21: Conn_02x01; PinHeader_1x02_P2.54mm_Vertical
J2: Conn_01x04; PinHeader_1x04_P2.54mm_Vertical
J4: Conn_01x06; PinHeader_1x06_P2.54mm_Vertical
J20: USB_B_Micro; USB_Mini-B_Lumberg_2486_01_Horizontal
JP3, JP4, JP5, JP6, JP7, JP8, JP9, JP10, JP11, JP12, JP13, JP14, JP15, JP16: Jumper_2_Open; SolderJumper-2_P1.3mm_Open_TrianglePad1.0x1.5mm
LD1: LD_BICOLOR_CMS; LD_BiCOLOR_CMS
Q2: Q_NPN_BEC; SOT-23
R1, R2, R3, R12: 10k; R_0603_1608Metric
R4, R23, R27: 4k7; R_0603_1608Metric
R5, R8, R13, R22: 22; R_0603_1608Metric
R6, R15, R71: 100k; R_0603_1608Metric
R7: 2k7; R_0603_1608Metric
R9, R11, R19, R20, R21, R25: 100; R_0603_1608Metric
R10: 36k; R_0603_1608Metric
R16: 1k5; R_0603_1608Metric
R17, R18: 0; R_0603_1608Metric
R24: 100; C_0603_1608Metric
R26: [N/A]; R_0603_1608Metric
U10: LD3985M33R_SOT23; SOT-23-5
U11: STM32F103CBTx; LQFP-48_7x7mm_P0.5mm
X1: Crystal; Resonator-2Pin_W8.0mm_H3.5mm

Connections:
+5VA: D3.2 (A), R7.2; also elsewhere on the board
+5VP: D2.2 (A), J20.1 (VBUS), R12.2; also elsewhere on the board
/Microcontroller_F1/OSC+: C3.2, U11.5 (PD0), X1.1
/Microcontroller_F1/OSC-: C8.1, U11.6 (PD1), X1.2
AIN_1: R9.1, R23.2, R27.2, U11.10 (PA0)
BOOT0: R6.1, U11.44 (BOOT0); also elsewhere on the board
GND: C1.2, C2.2, C3.1, C4.2, C5.2, C6.2, C7.2, C8.2, C9.2, C10.2, C11.2, C12.2, C13.2, J4.3, J11.1, J11.2, J12.1, J12.2, J20.5 (GND), J20.6 (Shield), J21.1, JP8.2 (B), JP11.2 (B), LD1.1, R1.1, R2.1, R3.1, R4.1, R6.2, R10.1, R15.1, R27.1, U10.2 (GND), U11.8 (VSSA), U11.20 (PB2), U11.23 (VSS), U11.35 (VSS), U11.47 (VSS); also elsewhere on the board
LED_STLINK: R20.1, R21.1, U11.30 (PA9)
MCO: JP16.2 (B); also elsewhere on the board
NRST: JP12.2 (B); also elsewhere on the board
unnamed: C2.1, C5.1, D2.1 (K), D3.1 (K), U10.1 (VIN), U10.3 (INH)
unnamed: C9.1, U10.4 (BYP)
unnamed: C10.1, JP16.1 (A), R25.1
unnamed: D1.1 (K), R9.2
unnamed: D1.2 (A), J4.1, R1.2
unnamed: J2.1, JP3.2 (B), JP4.1 (A)
unnamed: J2.2, JP5.2 (B), JP6.1 (A)
unnamed: J2.3, JP7.2 (B), JP8.1 (A)
unnamed: J2.4, JP9.2 (B), JP10.1 (A)
unnamed: J4.2, R5.2
unnamed: J4.4, R8.2
unnamed: J4.5, R13.2
unnamed: J4.6, R22.2
unnamed: J20.2 (D-), R18.2
unnamed: J20.3 (D+), R16.2, R17.2
unnamed: J20.4 (ID), R15.2
unnamed: J21.2, R26.1, U11.21 (PB10)
unnamed: LD1.2, R21.2
unnamed: LD1.3, R20.2
unnamed: LD1.4, R19.1
unnamed: Q2.1 (B), R10.2, R11.1, R12.1
unnamed: Q2.2 (E), R16.1
unnamed: R2.2, U11.3 (PC14)
unnamed: R3.2, U11.2 (PC13)
unnamed: R25.2, U11.29 (PA8)
PA2: JP13.2 (B); also elsewhere on the board
PA3: JP14.2 (B); also elsewhere on the board
PA13: JP9.1 (A); also elsewhere on the board
PA14: JP5.1 (A); also elsewhere on the board
PB3: JP15.2 (B); also elsewhere on the board
PWR_ENn: U11.28 (PB15); also elsewhere on the board
PWR_EXT: J1.2, R4.2, R7.1, U11.39 (PB3)
STM_JTCK: JP6.2 (B), U11.37 (PA14)
STM_JTMS: JP10.2 (B), U11.34 (PA13)
STM_RST: C6.1, JP11.1 (A), R71.1, U11.7 (NRST)
ST_LINK_RX: J3.2, JP13.1 (A), U11.13 (PA3)
ST_LINK_TX: J3.1, JP14.1 (A), U11.12 (PA2)
T_JTCK: JP3.1 (A), R5.1, U11.15 (PA5), U11.26 (PB13)
T_JTMS: JP7.1 (A), R8.1, R24.1, U11.27 (PB14)
T_NRST: JP12.1 (A), R13.1, U11.18 (PB0)
T_SWDIO_IN: R24.2, U11.25 (PB12)
T_SWO: JP15.1 (A), R22.1, U11.31 (PA10)
USB_DM: R17.1, U11.32 (PA11)
USB_DP: R18.1, U11.33 (PA12)
USB_RENUMn: R11.2, U11.38 (PA15)

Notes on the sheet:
RESERVED
DEFAULT
JUMPERS ON --> NUCLEO Selected
JUMPERS OFF --> ST-LINK Selected
USB ST-Link
PINY HIERARCHICZNE
PWR
good
Wired on Solder Side

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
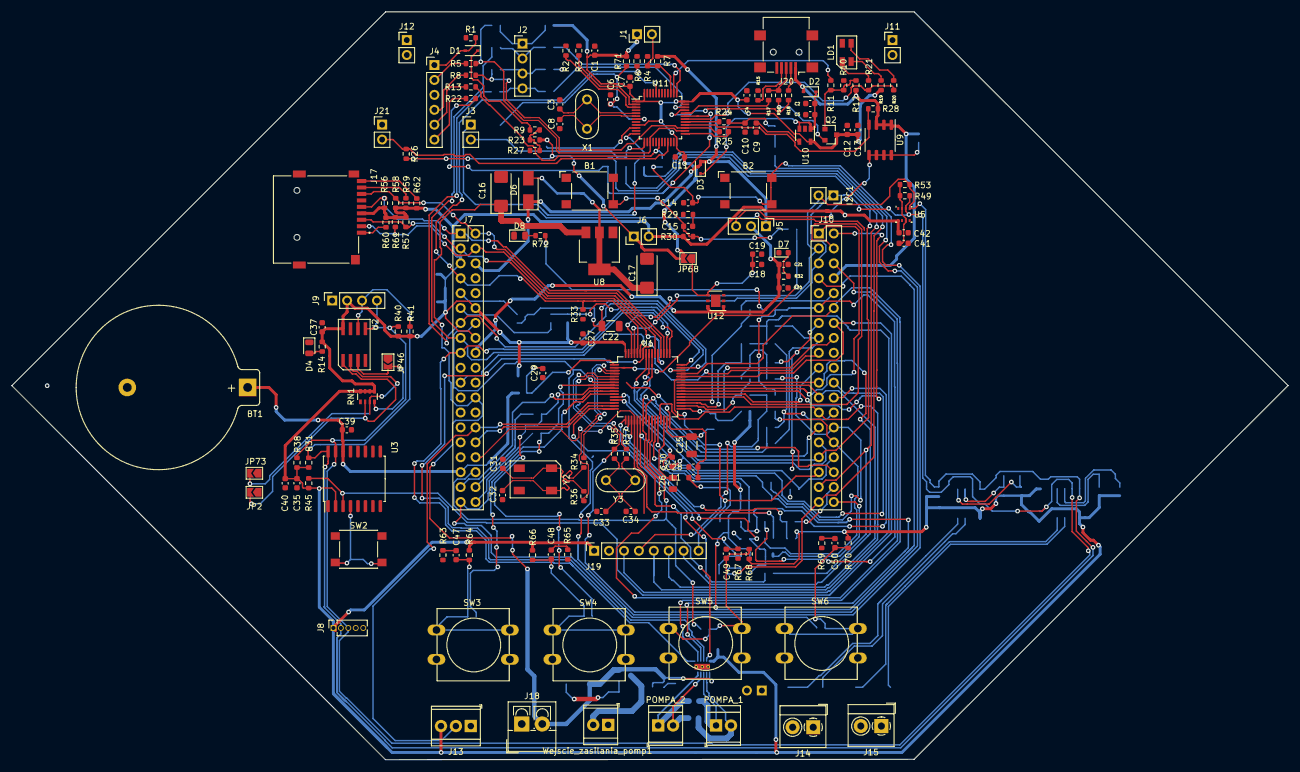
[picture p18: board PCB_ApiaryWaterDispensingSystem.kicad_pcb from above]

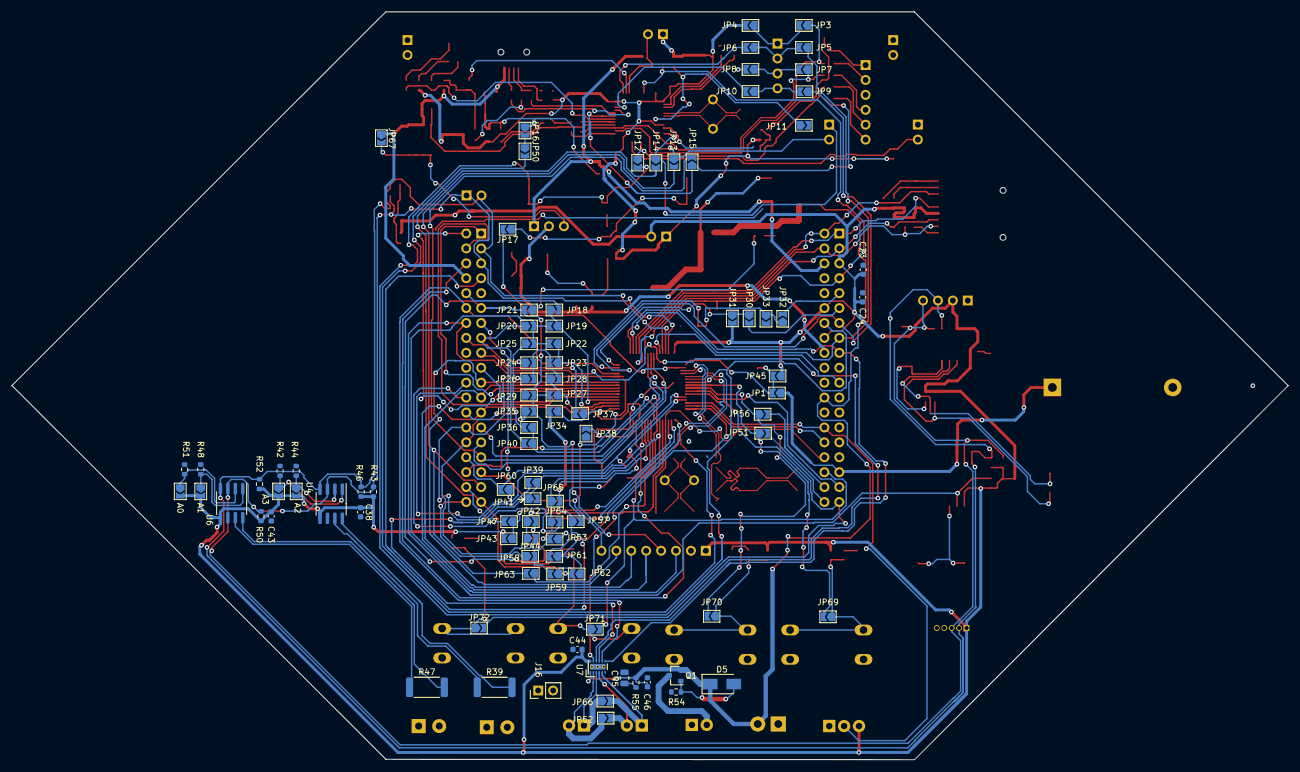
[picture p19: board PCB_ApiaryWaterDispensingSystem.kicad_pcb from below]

Board: 2 copper layers, 217.3 x 127.3 mm, 255 parts (94 on the bottom side), 180 nets.

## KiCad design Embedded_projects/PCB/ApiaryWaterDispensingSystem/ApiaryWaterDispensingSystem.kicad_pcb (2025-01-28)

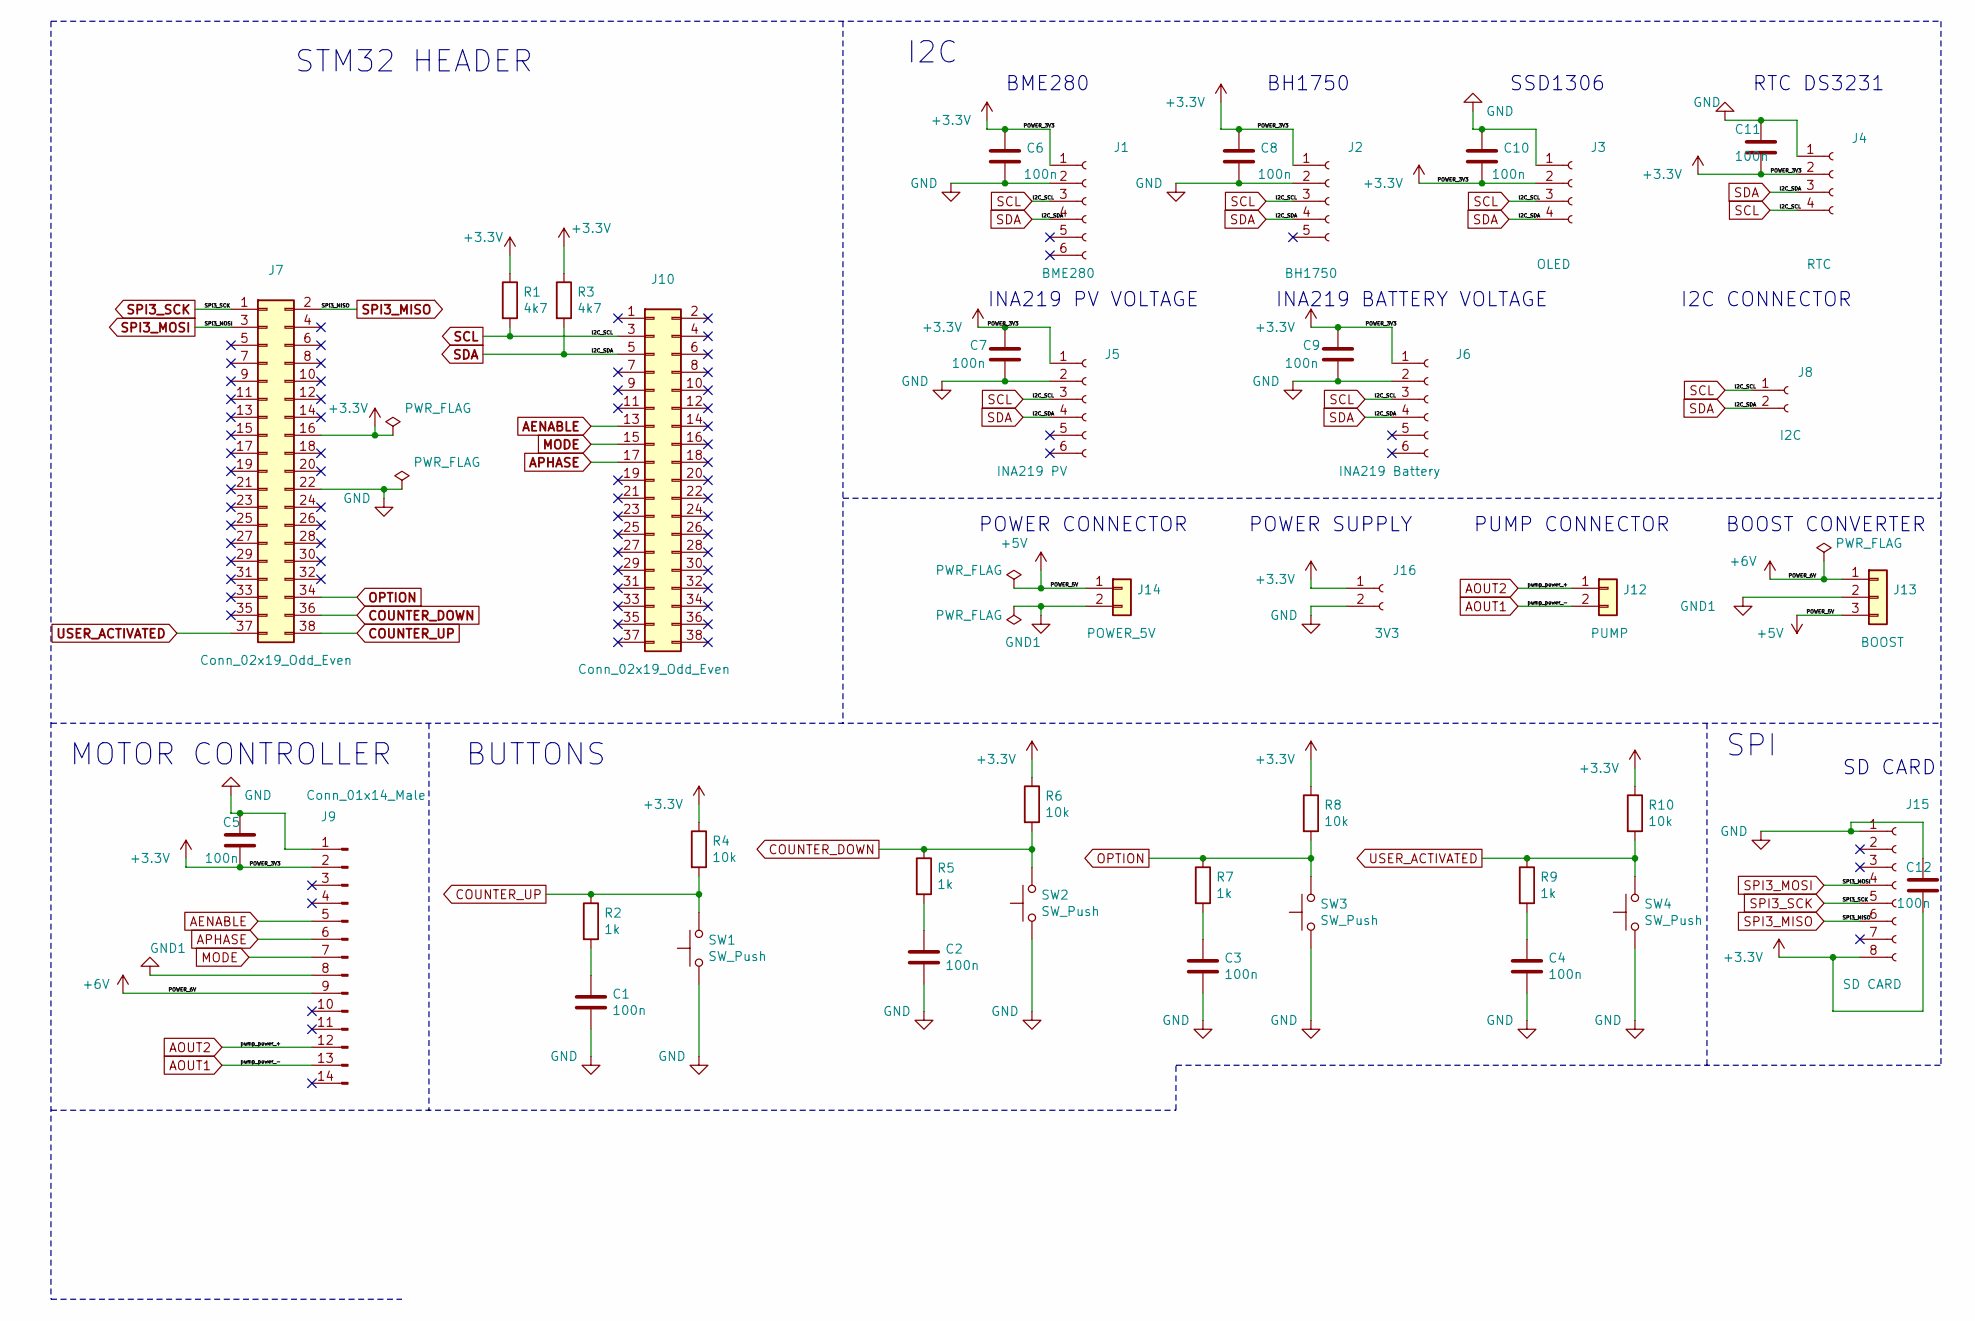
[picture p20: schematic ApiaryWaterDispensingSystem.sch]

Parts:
C1, C2, C3, C4, C5, C6, C7, C8, C9, C10, C11, C12: 100n; C_0805_2012Metric
J1: BME280; PinSocket_1x06_P2.54mm_Vertical_BME280
J2: BH1750; PinSocket_1x05_P2.54mm_Vertical
J3: OLED; PinSocket_1x04_P2.54mm_Vertical
J4: RTC; PinSocket_1x04_P2.54mm_Vertical_RTCDS3231
J5: INA219 PV; PinSocket_1x06_P2.54mm_Vertical
J6: INA219 Battery; PinSocket_1x06_P2.54mm_Vertical
J7, J10: Conn_02x19_Odd_Even; PinSocket_2x19_P2.54mm_Vertical
J8: I2C; PinSocket_1x02_P2.54mm_Vertical
J9: Conn_01x14_Male; PinSocket_1x07_P2.54mm_Vertical_DRV8835
J12: PUMP; TerminalBlock_TE_282834-2_1x02_P2.54mm_Horizontal
J13: BOOST; PinSocket_1x03_P2.00mm_Vertical
J14: POWER_5V; TerminalBlock_TE_282834-2_1x02_P2.54mm_Horizontal
J15: SD CARD; PinSocket_1x08_P2.54mm_Vertical_SD_CARD
J16: 3V3; PinSocket_1x02_P2.54mm_Vertical
R1, R3: 4k7; R_0805_2012Metric
R2, R5, R7, R9: 1k; R_0805_2012Metric
R4, R6, R8, R10: 10k; R_0805_2012Metric
SW1, SW2, SW3, SW4: SW_Push; SW_PUSH-12mm

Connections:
+3V3: C5.2, C6.1, C7.1, C8.1, C9.1, C10.2, C11.2, C12.2, J1.1, J2.1, J3.2, J4.2, J5.1, J6.1, J7.16, J9.2, J15.8, J16.1, R1.1, R3.1, R4.1, R6.1, R8.1, R10.1
+5V: J13.3, J14.1
+6V: J9.9, J13.1
AENABLE: J9.5, J10.13
AOUT1: J9.13, J12.2
AOUT2: J9.12, J12.1
APHASE: J9.6, J10.17
COUNTER_DOWN: J7.36, R5.1, R6.2, SW2.2
COUNTER_UP: J7.38, R2.1, R4.2, SW1.2
GND: C1.2, C2.2, C3.2, C4.2, C5.1, C6.2, C7.2, C8.2, C9.2, C10.1, C11.1, C12.1, J1.2, J2.2, J3.1, J4.1, J5.2, J6.2, J7.22, J9.1, J15.1, J16.2, SW1.1, SW2.1, SW3.1, SW4.1
GND1: J9.8, J13.2, J14.2
MODE: J9.7, J10.15
unnamed: C1.1, R2.2
unnamed: C2.1, R5.2
unnamed: C3.1, R7.2
unnamed: C4.1, R9.2
OPTION: J7.34, R7.1, R8.2, SW3.2
SCL: J1.3, J2.3, J3.3, J4.4, J5.3, J6.3, J8.1, J10.3, R1.2
SDA: J1.4, J2.4, J3.4, J4.3, J5.4, J6.4, J8.2, J10.5, R3.2
SPI3_MISO: J7.2, J15.6
SPI3_MOSI: J7.3, J15.4
SPI3_SCK: J7.1, J15.5
USER_ACTIVATED: J7.37, R9.1, R10.2, SW4.2

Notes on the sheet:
STM32 HEADER
I2C
BH1750
SSD1306
INA219 PV VOLTAGE
INA219 BATTERY VOLTAGE
SD CARD
RTC DS3231
BME280
PUMP CONNECTOR
I2C CONNECTOR
BOOST CONVERTER
SPI
POWER SUPPLY
BUTTONS
POWER CONNECTOR
MOTOR CONTROLLER

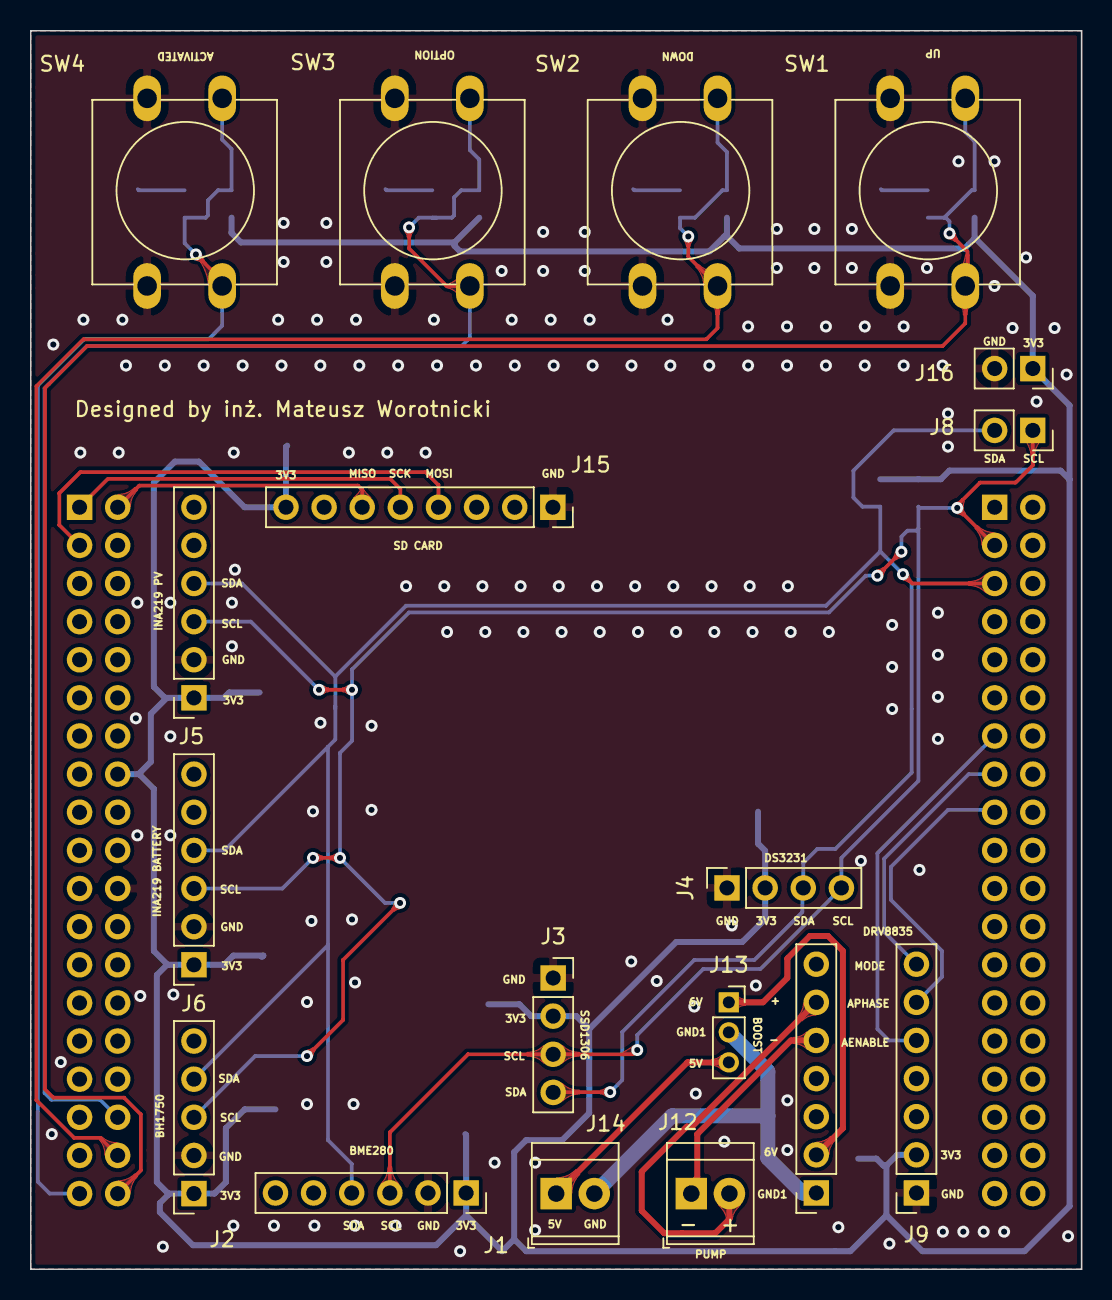
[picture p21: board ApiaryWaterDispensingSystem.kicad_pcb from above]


Board: 2 copper layers, 70.0 x 82.5 mm, 41 parts (24 on the bottom side), 23 nets.

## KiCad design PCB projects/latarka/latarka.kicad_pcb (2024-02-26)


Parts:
C1: 10u; C_0805_2012Metric_Pad1.18x1.45mm_HandSolder
C2: 4,7u; C_0805_2012Metric_Pad1.18x1.45mm_HandSolder
D1: LED_Small; LED_D8.0mm
J1, J1Bateria1: Conn_01x02; PinHeader_1x02_P2.54mm_Vertical
L1: 4,7u; cewka_m2
R1: 10k; R_0805_2012Metric_Pad1.20x1.40mm_HandSolder
R2: 4; R_0805_2012Metric_Pad1.20x1.40mm_HandSolder
U1: MCP1643xMS; MSOP-8_3x3mm_P0.65mm

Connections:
+1V5: C1.1, J1.2, J1Bateria1.2, L1.1, U1.8 (VIN)
GND: C1.2, C2.2, J1Bateria1.1, R1.2, R2.2, U1.6 (PGND), U1.7 (SGND)
unnamed: C2.1, D1.2 (A), U1.4 (VOUT)
unnamed: D1.1 (K), R2.1, U1.2 (VFB)
unnamed: J1.1, R1.1, U1.1 (EN)
unnamed: L1.2, U1.5 (SW)

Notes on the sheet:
Iled=0,12[V]/ Rset
R=4[Ohm]



Board: 2 copper layers, 9 parts (3 on the bottom side), 6 nets.

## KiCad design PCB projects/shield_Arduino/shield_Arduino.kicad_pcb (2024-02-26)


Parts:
C1, C3: 1nF; C_0805_2012Metric_Pad1.18x1.45mm_HandSolder
C2: 27n; C_0805_2012Metric_Pad1.18x1.45mm_HandSolder
C4: 56mF; C_0805_2012Metric_Pad1.18x1.45mm_HandSolder
C5: 1000uF; CP_Elec_10x10
D1, D2, D3, D4, D5, D6, D7, D8, D9: LED; LED_0805_2012Metric_Pad1.15x1.40mm_HandSolder
J1: Conn_01x10_Male; PinHeader_1x10_P2.54mm_Vertical
J2, J4: Conn_01x08_Male; PinHeader_1x08_P2.54mm_Vertical
J3: Conn_01x06_Male; PinHeader_1x06_P2.54mm_Vertical
J5: AudioJack2_SwitchT; Jack_3.5mm_Lumberg_150304_Horizontal
LS1: Speaker; TerminalBlock_Altech_AK300-2_P5.00mm
Q1: BCP56; SOT-223-3_TabPin2
R1: 13k; R_0805_2012Metric_Pad1.20x1.40mm_HandSolder
R2: 27k; R_0805_2012Metric_Pad1.20x1.40mm_HandSolder
R3: 1k6; R_0805_2012Metric_Pad1.20x1.40mm_HandSolder
R4: 3k; R_0805_2012Metric_Pad1.20x1.40mm_HandSolder
R5: 120; R_0805_2012Metric_Pad1.20x1.40mm_HandSolder
R6, R7, R8, R9, R10, R11, R12, R13, R14: 220; R_0805_2012Metric_Pad1.20x1.40mm_HandSolder
SW1, SW2, SW3, SW4, SW5, SW6, SW7, SW8: SWITCH; SW_PUSH_6mm_H5mm
U1: MCP6002-xSN; SOIC-8-1EP_3.9x4.9mm_P1.27mm_EP2.514x3.2mm

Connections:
+5V: C5.1, J4.5, Q1.2 (C), R6.1, R7.1, R8.1, R9.1, R10.1, R11.1, R12.1, R13.1, R14.1, U1.8 (V+)
/AUDIO_WAVE: C4.1, R5.2, U1.6 (-), U1.7
AUDIO_PWM: J2.7, R1.2
BTN_1: J2.1, R14.2, SW8.2 (B)
BTN_2: J2.2, R13.2, SW7.2 (B)
BTN_3: J2.3, R12.2, SW6.2 (B)
BTN_4: J2.4, R11.2, SW5.2 (B)
BTN_5: J2.5, R10.2, SW4.2 (B)
BTN_6: J2.6, R9.2, SW3.2 (B)
BTN_7: J2.8, R8.2, SW2.2 (B)
BTN_8: J1.1, R7.2, SW1.2 (B)
GND: C1.2, C3.2, C5.2, D1.1 (K), D2.1 (K), D3.1 (K), D4.1 (K), D5.1 (K), D6.1 (K), D7.1 (K), D8.1 (K), D9.1 (K), J1.7, J4.6, J4.7, J5.S, LS1.1, U1.4 (V-)
unnamed: C1.1, R2.1, U1.3 (+)
unnamed: C2.1, R3.2, U1.1, U1.2 (-)
unnamed: C2.2, R1.1, R2.2
unnamed: C3.1, R4.1, U1.5 (+)
unnamed: C4.2, R3.1, R4.2
unnamed: D1.2 (A), R6.2
unnamed: D2.2 (A), SW1.1 (A)
unnamed: D3.2 (A), SW2.1 (A)
unnamed: D4.2 (A), SW3.1 (A)
unnamed: D5.2 (A), SW4.1 (A)
unnamed: D6.2 (A), SW5.1 (A)
unnamed: D7.2 (A), SW6.1 (A)
unnamed: D8.2 (A), SW7.1 (A)
unnamed: D9.2 (A), SW8.1 (A)
unnamed: J5.T, Q1.3 (E)
unnamed: J5.TN, LS1.2
unnamed: Q1.1 (B), R5.1

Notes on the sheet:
ARDUINO HEADER
4-POLE CHEBYSHEV LOW-PASS FILTER WITH 10 KHZ CUT-OFF
KEYBOARD
POWER-ON INDICATOR
OP-AMP (U1) POWER SUPPLY
POWER STAGE
NOTE: R5 PROTECTS OP_AMP OUTPUT FROM SHORU CURCUIT.CAN BE REPLACED BY ZERO OHM IF MORE POWER IS REQUIRED


Board: 2 copper layers, 69.6 x 53.3 mm, 45 parts (0 on the bottom side), 29 nets.

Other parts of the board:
e: MountingHole_3.2mm_M3

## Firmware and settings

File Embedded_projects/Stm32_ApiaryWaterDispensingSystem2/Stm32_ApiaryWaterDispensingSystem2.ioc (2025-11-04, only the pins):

Mcu.UserName=STM32F411RETx
PA0-WKUP.Signal=ADCx_IN0
PA10.GPIO_Label=BACKLIGHT
PA10.Signal=GPIO_Output
PA11.GPIO_Label=SQW
PA11.Signal=GPIO_Input
PA12.GPIO_Label=BPHASE
PA12.Signal=GPIO_Output
PA13.GPIO_Label=TMS
PA13.Signal=SYS_JTMS-SWDIO
PA14.GPIO_Label=TCK
PA14.Signal=SYS_JTCK-SWCLK
PA15.GPIO_Label=BENABLE
PA15.Signal=S_TIM2_CH1_ETR
PA2.GPIO_Label=USART_TX
PA2.Signal=USART2_TX
PA3.GPIO_Label=USART_RX
PA3.Signal=USART2_RX
PA5.GPIO_Label=LD2 [Green Led]
PA5.Signal=GPIO_Output
PA6.GPIO_Label=AENABLE
PA6.Signal=S_TIM3_CH1
PA7.GPIO_Label=MODE
PA7.Signal=GPIO_Output
PA8.GPIO_Label=DC_DISPLAY
PA8.Signal=GPIO_Output
PA9.GPIO_Label=RST_DISPLAY
PA9.Signal=GPIO_Output
PB0.GPIO_Label=B3
PB0.Signal=GPIO_Input
PB10.GPIO_Label=SPI2_CS
PB10.Signal=GPIO_Output
PB13.Signal=SPI2_SCK
PB15.Signal=SPI2_MOSI
PB3.GPIO_Label=SWO
PB3.Signal=SYS_JTDO-SWO
PB6.GPIO_Label=APHASE
PB6.Signal=GPIO_Output
PB8.Signal=I2C1_SCL
PB9.Signal=I2C1_SDA
PC0.GPIO_Label=B1
PC0.Signal=GPIO_Input
PC1.GPIO_Label=B2
PC1.Signal=GPIO_Input
PC10.Signal=SPI3_SCK
PC11.Signal=SPI3_MISO
PC12.Signal=SPI3_MOSI
PC14-OSC32_IN.Signal=RCC_OSC32_IN
PC15-OSC32_OUT.Signal=RCC_OSC32_OUT
PC2.Signal=SPI2_MISO
PC3.GPIO_Label=B4
PC3.Signal=GPIO_Input
PD2.GPIO_Label=SPI3_CS
PD2.Signal=GPIO_Output

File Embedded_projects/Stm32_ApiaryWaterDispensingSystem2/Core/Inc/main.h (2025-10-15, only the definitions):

#define B1_Pin GPIO_PIN_0
#define B1_GPIO_Port GPIOC
#define B2_Pin GPIO_PIN_1
#define B2_GPIO_Port GPIOC
#define B4_Pin GPIO_PIN_3
#define B4_GPIO_Port GPIOC
#define USART_TX_Pin GPIO_PIN_2
#define USART_TX_GPIO_Port GPIOA
#define USART_RX_Pin GPIO_PIN_3
#define USART_RX_GPIO_Port GPIOA
#define LD2_Pin GPIO_PIN_5
#define LD2_GPIO_Port GPIOA
#define AENABLE_Pin GPIO_PIN_6
#define AENABLE_GPIO_Port GPIOA
#define MODE_Pin GPIO_PIN_7
#define MODE_GPIO_Port GPIOA
#define B3_Pin GPIO_PIN_0
#define B3_GPIO_Port GPIOB
#define SPI2_CS_Pin GPIO_PIN_10
#define SPI2_CS_GPIO_Port GPIOB
#define SQW_Pin GPIO_PIN_11
#define SQW_GPIO_Port GPIOA
#define BPHASE_Pin GPIO_PIN_12
#define BPHASE_GPIO_Port GPIOA
#define TMS_Pin GPIO_PIN_13
#define TMS_GPIO_Port GPIOA
#define TCK_Pin GPIO_PIN_14
#define TCK_GPIO_Port GPIOA
#define BENABLE_Pin GPIO_PIN_15
#define BENABLE_GPIO_Port GPIOA
#define SPI3_CS_Pin GPIO_PIN_2
#define SPI3_CS_GPIO_Port GPIOD
#define SWO_Pin GPIO_PIN_3
#define SWO_GPIO_Port GPIOB
#define APHASE_Pin GPIO_PIN_6
#define APHASE_GPIO_Port GPIOB

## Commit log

2024-02-26 Create PCB projects
2024-02-26 -added KiCad project
    [shield_Arduino-B_Cu.gbr, shield_Arduino-B_Mask.gbr, shield_Arduino-B_Paste.gbr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]
2024-02-26 adding a flashlight design
    -Thanks to the integrated circuit, the system is able to operate at a lower battery cell voltage.
    [latarka.kicad_pcb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]
2024-02-29 + project configuration
    +added bh1750, bme280,ssd1306
    +configuration RTC
    +led blinking
2024-02-29 +SSD1306 task
    checking i2c communication
2024-03-20 +bugs fixes
    +added project, which is connecting with stm32f411re
    [GFX_BW.h, Stm32_ApiaryWaterDispensingSystem2.ioc, bh1750.c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]
2024-03-20 + activate the alarm correctness
    possibility of changing the pump activation for a specified number of minutes from 1 to 59
    - cyclical settings for turning on the pump after the alarm is triggered from 8 a.m. to 10 p.m
    [Stm32_ApiaryWaterDispensingSystem2.ioc, main.h]
2024-04-07 +update projects
    [ApiaryWaterDispensingSystem.kicad_pcb, ApiaryWaterDispensingSystem.sch]
2024-06-25 Update Kicad
    +update eeschema
2024-07-11 +update project
    positive test
    [ApiaryWaterDispensingSystem-B_Cu.gbr, ApiaryWaterDispensingSystem-B_Mask.gbr, ApiaryWaterDispensingSystem-B_Paste.gbr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]
2025-01-28 changes projects
    [ApiaryWaterDispensingSystem-B_Cu.gbr, ApiaryWaterDispensingSystem-B_Mask.gbr, ApiaryWaterDispensingSystem-B_Paste.gbr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]
2025-02-04 added machine states in file : button.c and button.h #7
2025-02-22 modfied button.h button.c freertos.c and main.c -> change of control user
2025-03-07 development of second protoype #3
    [MPPT.sch, PCB_ApiaryWaterDispensingSystem.kicad_pcb, PCB_ApiaryWaterDispensingSystem.sch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]
2025-03-14 added file ds3231.sch #3
    [PCB_ApiaryWaterDispensingSystem.sch, ds3231.sch, microcontroller.sch]
2025-03-20 added BME280 sensor to the project , #3
    [PCB_ApiaryWaterDispensingSystem.sch, ds3231.sch, microcontroller.sch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]
2025-03-29 added x-tal and his footprints for microcontroller schematics, user button
    [MPPT.sch, PCB_ApiaryWaterDispensingSystem.sch, SPI.sch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]
2025-03-30 stm32f411re completed schematic
    [MPPT.sch, Microcontroller_F1.sch, PCB_ApiaryWaterDispensingSystem.sch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]
2025-03-31 added elements of stm32F103CBT6
2025-04-01 F1 completed
    [Microcontroller_F1.sch]
2025-04-03 added changes of Microntroller_F4 ->global variables #3
    [Microcontroller_F1.sch, microcontroller_F4.sch]
2025-06-24 added lot of changes to project #3
    [Buttons.sch, MPPT.sch, Microcontroller_F1.sch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]
2025-10-15 Many design changes have been added over the past few months #3
    [Buttons.sch, Display.sch, MPPT.sch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]
2025-11-04 All signal has been routed, the analog part needs to be completed
    [Buttons.sch, Display.sch, Microcontroller_F1.sch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]
2025-11-14 update html in readme.RST and improved PCb #3
    [PCB_ApiaryWaterDispensingSystem.kicad_pcb, microcontroller_F4.sch]

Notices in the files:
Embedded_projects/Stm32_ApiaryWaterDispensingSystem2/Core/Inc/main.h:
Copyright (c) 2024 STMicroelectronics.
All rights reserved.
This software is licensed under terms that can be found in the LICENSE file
